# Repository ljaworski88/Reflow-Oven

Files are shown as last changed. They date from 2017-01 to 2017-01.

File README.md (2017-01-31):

# Reflow-Oven
My take on the diy relfow oven, inspired by the design by Karl Pitrich (karl@pitrich.com).

This reflow oven is still undergoing development, slowly, but works well enough to
bake some ICs. The reflowreader.py program is used to get a graphical output of the 
current temperature and setpoint (you will need to know which serial port the arduino
is connected to), it is written in python 2.7 and will need the correct interpreter.

The door does not open on its own yet and cannot autotune the PID but it can detect
the mains power frequency. The user will need to open the door manually for cooling.
Also fan control has not been implemented as my oven did not have any of that fanciness.

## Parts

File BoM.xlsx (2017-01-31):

Mfcr Part # | Description | cost | link
MAX31855 | Thermocouple IC | $4.50 | http://www.digikey.com/product-detail/en/MAX31855KASA%2B/MAX31855KASA%2B-ND/2591564
WB26K5069 | Convection Fan | $31.00 | http://www.ebay.com/itm/WB26K5069-GE-RANGE-OVEN-CONVECTION-MOTOR-FAN-/131715413430

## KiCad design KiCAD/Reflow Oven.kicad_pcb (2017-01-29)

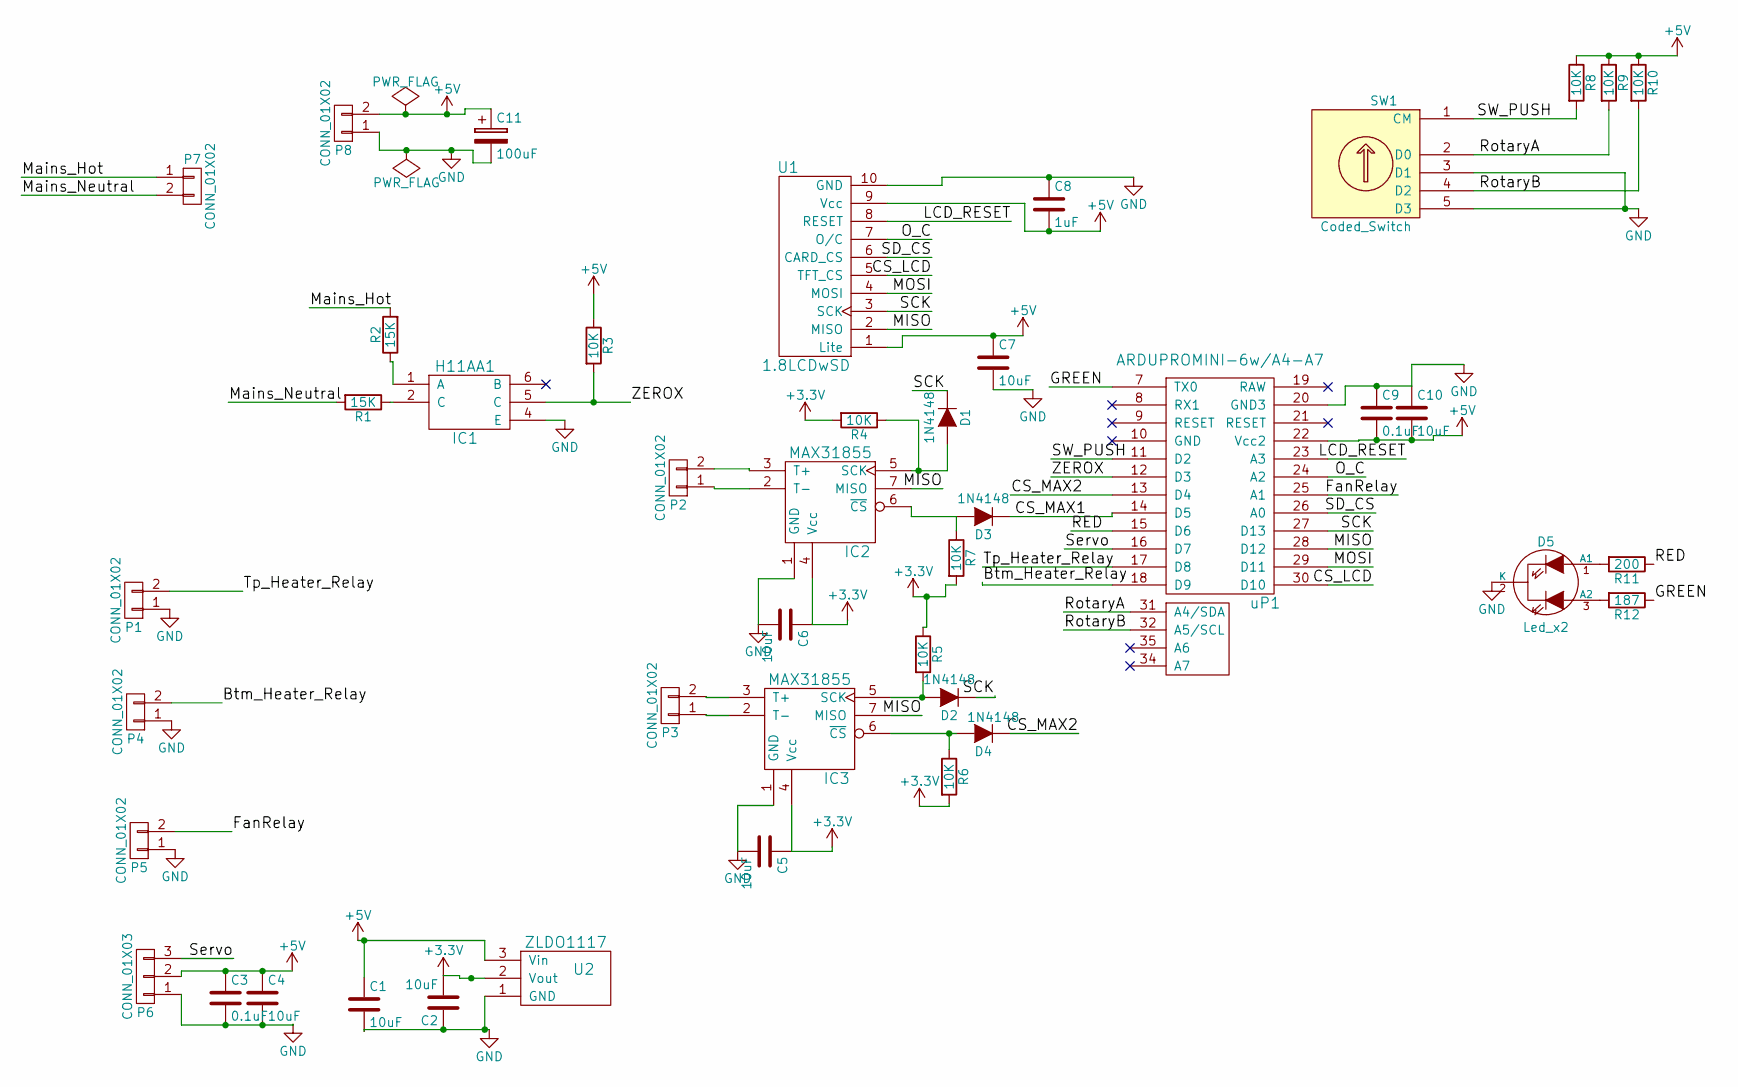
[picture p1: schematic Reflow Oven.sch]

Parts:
C1, C2, C4, C5, C6, C7, C10: 10uF; C_0402
C3, C9: 0.1uF; C_0402
C8: 1uF; C_0402
C11: 100uF; 10mm-THRU-ALUMINUM-CAP
D1, D2, D3, D4: 1N4148; SOD-123
D5: Led_x2; LED-5MM-3
IC1: H11AA1; SOIC-6
IC2, IC3: MAX31855; SOIC8
P1, P2, P3, P4, P5, P8: CONN_01X02; TerminalBlock_Pheonix_MPT-2.54mm_2pol
P6: CONN_01X03; SIP3
P7: CONN_01X02; TerminalBlock_Pheonix_PT-3.5mm_2pol
R1, R2: 15K; 1206
R3, R4, R5, R6, R7, R8, R9, R10: 10K; 0402
R11: 200; 0402
R12: 187; 0402
SW1: Coded_Switch; SF-ROTARY-ENCODER
U1: 1.8LCDwSD; 1X10
U2: ZLDO1117; DPAK
uP1: ARDUPROMINI-6w/A4-A7; ArduProMini-6

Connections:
+3V3: C2.2, C5.1, C6.1, IC2.4 (Vcc), IC3.4 (Vcc), R4.2, R5.1, R6.2, R7.2, U2.2 (Vout)
+5V: C1.1, C3.1, C4.1, C7.1, C8.2, C9.2, C10.2, C11.1, P6.2, P8.2, R3.1, R8.1, R9.1, R10.1, U1.1 (Lite), U1.9 (Vcc), U2.3 (Vin), uP1.22 (Vcc2)
/Btm_Heater_Relay: P4.2, uP1.18 (D9)
/CS_LCD: U1.5 (TFT_CS), uP1.30 (D10)
/CS_MAX1: D3.1 (K), uP1.14 (D5)
/CS_MAX2: D4.1 (K), uP1.13 (D4)
/FanRelay: P5.2, uP1.25 (A1)
/GREEN: R12.1, uP1.7 (TX0)
/LCD_RESET: U1.8 (RESET), uP1.23 (A3)
/MISO: IC2.7 (MISO), IC3.7 (MISO), U1.2 (MISO), uP1.28 (D12)
/MOSI: U1.4 (MOSI), uP1.29 (D11)
/Mains_Hot: P7.1, R2.2
/Mains_Neutral: P7.2, R1.2
/O_C: U1.7 (O/C), uP1.24 (A2)
/RED: R11.1, uP1.15 (D6)
/RotaryA: R9.2, SW1.2 (D0), uP1.31 (A4/SDA)
/RotaryB: R10.2, SW1.4 (D2), uP1.32 (A5/SCL)
/SCK: D1.1 (K), D2.1 (K), U1.3 (SCK), uP1.27 (D13)
/SD_CS: U1.6 (CARD_CS), uP1.26 (A0)
/SW_PUSH: R8.2, SW1.1 (CM), uP1.11 (D2)
/Servo: P6.3, uP1.16 (D7)
/Tp_Heater_Relay: P1.2, uP1.17 (D8)
/ZEROX: IC1.5 (C), R3.2, uP1.12 (D3)
GND: C1.2, C2.1, C3.2, C4.2, C5.2, C6.2, C7.2, C8.1, C9.1, C10.1, C11.2, D5.2 (K), IC1.4 (E), IC2.1 (GND), IC3.1 (GND), P1.1, P4.1, P5.1, P6.1, P8.1, SW1.3 (D1), SW1.5 (D3), U1.10 (GND), U2.1 (GND), uP1.20 (GND3)
unnamed: D1.2 (A), IC2.5 (SCK), R4.1
unnamed: D2.2 (A), IC3.5 (SCK), R5.2
unnamed: D3.2 (A), IC2.6 (~CS), R7.1
unnamed: D4.2 (A), IC3.6 (~CS), R6.1
unnamed: D5.1 (A1), R11.2
unnamed: D5.3 (A2), R12.2
unnamed: IC1.1 (A), R2.1
unnamed: IC1.2 (C), R1.1
unnamed: IC2.2 (T-), P2.1
unnamed: IC2.3 (T+), P2.2
unnamed: IC3.2 (T-), P3.1
unnamed: IC3.3 (T+), P3.2

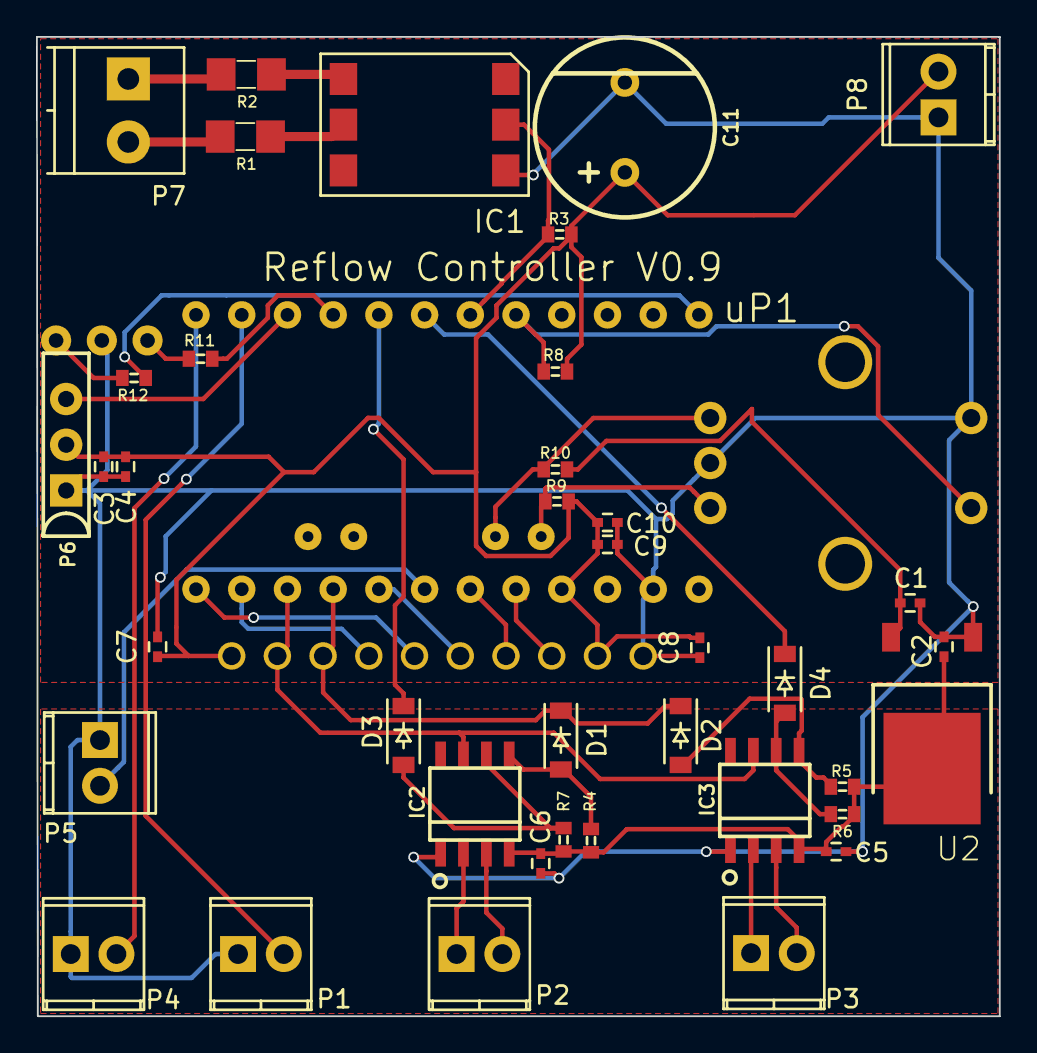
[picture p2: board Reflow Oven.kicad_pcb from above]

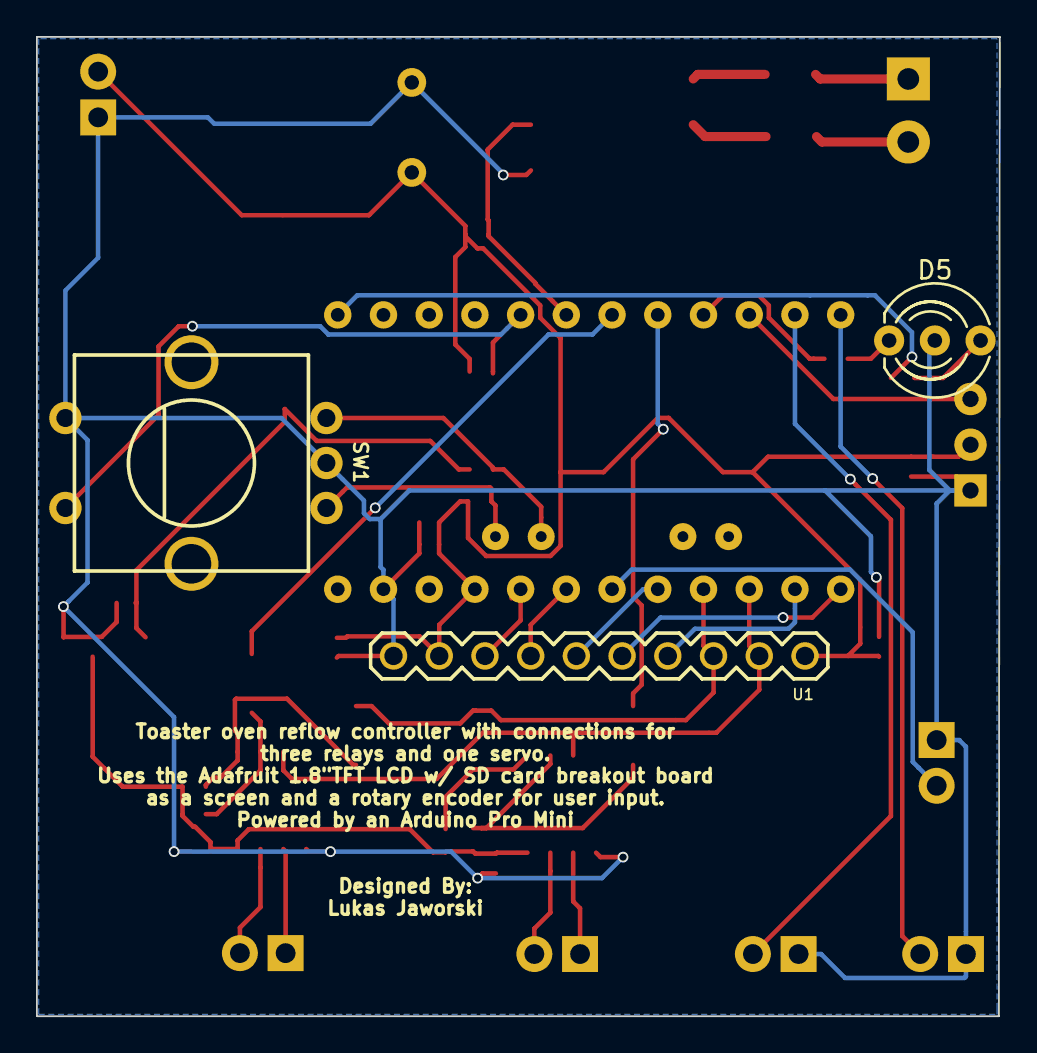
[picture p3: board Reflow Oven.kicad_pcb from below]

Board: 2 copper layers, 53.5 x 54.4 mm, 43 parts (3 on the bottom side), 36 nets.

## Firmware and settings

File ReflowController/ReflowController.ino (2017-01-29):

/* Reflow Oven Controller
 2016 Lukas Jaworski
 based on the Reflow Controller by Karl Pitrich
  v 0.7.2
*/ 

//-----------------------------------------------------------------------------
//Optional Defines
//-----------------------------------------------------------------------------

// #define AUTOPID true // autotune PID parameters
#define ZERO_X_CALIBRATION True

#ifdef ZERO_X_CALIBRATION
	#define CALIBRATION_CYCLES 12 //set how many calibration cyles are desired, the first two and last readings are thrown out due to inconsistant readings because of intialization and shutdown
#endif

//-----------------------------------------------------------------------------
//File Depencencies
//-----------------------------------------------------------------------------

#include <avr/io.h>
#include <PID_v1.h>
#include <Adafruit_GFX.h>
#include <Adafruit_ST7735.h>
#include <SPI.h>
#include <TimerOne.h>
#include <Servo.h>
#ifdef AUTOPID
	#include <PID_AutoTune_v0.h>
#endif

// ----------------------------------------------------------------------------
// Hardware Configuration
// ----------------------------------------------------------------------------

// 1.8" TFT via SPI

#define LCD_CS	10
#define LCD_OC	A2
#define LCD_RST	A3
#define SD_CS	A0


// Thermocouples

// Thermocouple via SPI-MAX31855
#define THERMOCOUPLE1_CS	5
#define THERMOCOUPLE2_CS	4//include later

//  Heater Solid State Relays

#define PIN_HEATER_TOP		9// SSR for the top heating elements- separate later
#define PIN_HEATER_BOTTOM	8// SSR for the bottom heating elements

//fan relay &| servo 

#define PIN_FAN		A1// SSR for the fan- This reflow oven has no fan
#define PIN_SERVO	7// servo control signal

// Rotary Encoder

#define ROTARY_A 	A4
#define ROTARY_B	A5
#define SW_PUSH		2

// Zero Crossing Detector

#define PIN_ZX		3 // pin for zero crossing detector
#define INT_ZX		digitalPinToInterrupt(PIN_ZX) // interrupt for zero crossing detector

// Indicator Light

#define RED		6
#define GREEN	0

//-----------------------------------------------------------------------------
// Profiles
//-----------------------------------------------------------------------------
typedef struct reflowProfile { //a complete reflow profile in terms temperaturs and temperature rates
	double	rampSoakRate;	//ramp to soak in degC/s
	double	soakLowTemp;	//temp in degC to start soak
	double	soakRate;		//gentle ramp during soak in degC/s
	double	soakHighTemp;	//temp in degC to stop soak and ramp to peak
	double	rampPeakRate;	//ramp to peak in degC/s
	double	peakTemp;		//peak temp in degC
	double	coolDownRate;	//cooling rate in degC/s
	double	safeTemp;		//temp in degC where oven is cool enough to work with
} reflowProfile;

typedef struct PID_constants { //a collection of PID constants
	double	Kp;
	double	Ki;
	double	Kd;
} PID_constants;

typedef struct PIDprofile { //a profile to adjust PID constants during reflow
	PID_constants	rampSoak;
	PID_constants	soak;
	PID_constants	rampPeak;
	PID_constants	coolDown;
} PIDprofile;

typedef struct currentParameters { //PID Input, Setpoint, and Output respectively
	double	avgTemp;
	double	setpoint;
	double	PID_output;
} currentParameters;

//-----------------------------------------------------------------------------
//TYPEDEFS
//-----------------------------------------------------------------------------

typedef enum reflowState { //state machine
	None     = 0,
	Idle     = 1,
	
	RampToSoak = 10,
	Soak,
	RampUp,
	RampDown,
	CoolDown,
	
	Complete = 20,
	
	Tune = 30
} reflowState;

typedef enum errorCode { //handle all currently known error states of the reflow oven
	NoError = 0,
	UnderTemp,
	OverTemp,
	BadReadings,
	NoMAX,
	VccShort,
	GndShort,
	OpenCircuit
} errorCode;


typedef union MAX31855_t { // thermocouple temp & status data, directly from the MAX31855
	uint32_t	value;
	uint8_t		bytes[4];

/*bits 31-18 hold the thermocouple data, 
bit 16 holds the fault bit (0 if no fault and 1 if there is one), this is not used at all in the code,
bits 15-4 hold the cold junction temperature, 
bits 2-0 explain the fault
*/   
} MAX31855_t;
 

typedef struct Thermocouple { // processed thermocouple data, status, and CS pin of the MAX31855
	double	temperature;
	uint8_t	stat;
	uint8_t	chipSelect;
} Thermocouple;

typedef struct rollingAvg { //holds the last ten actual temperature readings used in claclulating the rolling average, and keeps track of which position in the array needs to be updated next
	double	temps[10];
	uint8_t	position = 0;
} rollingAvg;

typedef struct cycleCount {//the "cycle counter" is how the PID output is translated into heater on/off times
	uint8_t	tensPlace;
	uint8_t	thirds;
	uint8_t	positionThirds;
	uint8_t	positionTens;
} cycleCount;

//-------------------------------------------------------------------------------
//Global Variables
//-------------------------------------------------------------------------------

const uint8_t		uSecPerTick = 100; //sets the timer tick rate that is used throughout the program, if you want to change this go over the code very carefully, especially the ISRs
const double		uSecPerSec = 0.0001;//conversion factor for the timer 0.0001sec = 100 usec
const uint32_t		updateTime = 10000; //update the setpoints every 1s - the updateTime variable is tied to the 100usec counter

volatile bool       cycleFinished = true; //indicates if the current "PWM" cycle is finished
volatile bool		offCounter = false; //the state of the countdown timer to turn off the SSR.
volatile uint8_t	offTimerTicks = 0;
volatile uint32_t	timerTicks = 0; //100usec timer keeper (no overflow detection)
// volatile uint32_t	zeroXticks = 0; //counts the zero crossing events, used in PID control
uint32_t			lastTimerTicks = 0;
uint32_t			lastPIDticks = 0;//used to ensure that the PID computes every time a heating "cycle" is finnished
uint8_t				usecPerZX = 83;//8.3ms (or 83 ticks @ 100us/tick) between ZeroX for 60Hz mains, 
									//sub in 10 for 50Hz. 
									//This value will be updated if a calibration is performed.
Thermocouple		thermoInput1; //intialize thermocouple 1
// Thermocouple		thermoInput2; //intialize thermocouple 2
uint8_t				servoPos = 0;
Servo				doorServo;
const uint32_t 		thermoUpdateTime = 250;//checks the temperature every 25ms so that it doesn't over tax the thermocouple IC
uint32_t			lastThermoUpdate;
reflowProfile		curProfile = {1.1, 135.0, 0.6, 165.0, 1.3, 225.0, 2.0, 50.0}; //the current reflow profile (also the only)
PIDprofile			curPIDprofile = {{1.1, 0.5, 30},{1.0, 0.1, 35.0},{3.0, 0.5, 5.0},{7.0, 0.01, 2.0}}; /*{{1.1, 0.101, 17.0},{1.0, 0.1, 18.0},{1.1, 0.1, 17.0},{7.0, 0.01, 2.0}}; //Profile of PID constants */
currentParameters	curParameters; //the current temp, setpoint, and pid output
reflowState			curOvenState = None; //current phase of the reflow cycle
rollingAvg			curRollingAvg; //a collection of past temp readings used in the rolling average
volatile cycleCount	cycleCounter = {0, 0, 0, 0}; //used to control heater on/off timings
volatile errorCode	curError = NoError;//Error code variable that handles all errors in the machine

PID					tempPID(&(curParameters.avgTemp),&(curParameters.PID_output),&(curParameters.setpoint),curPIDprofile.rampSoak.Kp,curPIDprofile.rampSoak.Kp,curPIDprofile.rampSoak.Kp,DIRECT);

#ifdef ZERO_X_CALIBRATION //These additional variables will be needed only if a ZeroX calibration is performed.
	volatile uint16_t	calibrationCycle = 0;
	volatile uint32_t	lastCalibrationTicks = 0;
	bool				calibrationFinished = false;
	uint16_t			calibrationArray[CALIBRATION_CYCLES];
	double				calibrationAvg = 0.0;
#endif

//-----------------------------------------------------------------------------
//FUNCTIONS
//-----------------------------------------------------------------------------

void readThermocouple(Thermocouple* input, volatile errorCode& ErrorCode) { //function to read the data from the MAX31855 and handle any errors that may arrise
	MAX31855_t readSensor;

	// uint8_t lcdState = digitalRead(LCD_CS);
	// digitalWrite(LCD_CS, HIGH);
	SPI.beginTransaction(SPISettings(4000000,MSBFIRST,SPI_MODE0));
	digitalWrite(input->chipSelect, LOW);
	for (int8_t i = 3; i >= 0; i--){
		readSensor.bytes[i] = SPI.transfer(0);
	}
	digitalWrite(input->chipSelect, HIGH);
	SPI.endTransaction();
	if (readSensor.value == 0){ //if nothing but zeroes is read then the MAX31855 is not connected or there is something seriously wrong, error is thrown
		ErrorCode = NoMAX;
	return;
	}
	input->stat = readSensor.bytes[0] & 0b111;
	if (input->stat){//this is the error handling portion which reads the MAX31855 error codes and passes them along to the main program
		switch (input->stat) {
			case 0b001:
				ErrorCode = OpenCircuit;
				return;
			case 0b010:
				ErrorCode = GndShort;
				return;
			case 0b100:
				ErrorCode = VccShort;
				return;
		}
	}
	uint16_t value = (readSensor.value >> 18) & 0x3FFF; //shift to the correct alignment for the temp data  
	input->temperature = (double) value * 0.25;
	// digitalWrite(LCD_CS, lcdState);
}

void openDoor(void){ 
	//use servo to open door as much as the servo will allow, also turns on a red indicator led
	digitalWrite(RED, HIGH);
	for (servoPos; servoPos<180; servoPos++){
		doorServo.write(servoPos);
		delay(100);
	}
}

void closeDoor(void){
	//use servo to fully close door
	for (servoPos; servoPos>0; servoPos--){
		doorServo.write(servoPos);
		delay(100);
	}
	
}

void indicateDone(bool errorFlag = false){//currently a dummy function
	//indicate that the reflow is complete (Use LED AND buzzer to indicate that reflow is complete)
	
}

void updateSetpoints(reflowState& ovenState, reflowProfile Profile, currentParameters& Params, PID& PID, PIDprofile PIDprofile){ //This function updates the setpoints of the reflow profile at the specified updateTime (which is counted in 100usec ticks)
	uint32_t timeSinceUpdate = timerTicks-lastTimerTicks;
	if (timeSinceUpdate>updateTime){//checks to see if there has been enough time since the last update to once again update the setpoints.
		if (ovenState>Idle && ovenState<RampDown){//Checks the reflow to see if it is in the heat up phase and adjusts the setpoints according to the programed profile.
			switch(ovenState) {
				case RampToSoak:
					Params.setpoint += Profile.rampSoakRate*double(timeSinceUpdate)*(uSecPerSec);
					if (Params.setpoint > Profile.soakLowTemp){
						ovenState = Soak;
						PID.SetTunings(curPIDprofile.soak.Kp,curPIDprofile.soak.Kp,curPIDprofile.soak.Kp);
					}
				break;
				
				case Soak:
					Params.setpoint += Profile.soakRate*double(timeSinceUpdate)*(uSecPerSec);
					if (Params.setpoint > Profile.soakHighTemp){
						ovenState = RampUp;
						PID.SetTunings(curPIDprofile.rampPeak.Kp,curPIDprofile.rampPeak.Kp,curPIDprofile.rampPeak.Kp);
					}
				break;
				
				case RampUp:
					Params.setpoint += Profile.rampPeakRate * double(timeSinceUpdate)*(uSecPerSec);
					if (Params.setpoint > (Profile.peakTemp - 5.0)){
						PID.SetMode(MANUAL);
						Params.PID_output = 0;
					}
					if (Params.setpoint > Profile.peakTemp){
						openDoor();
						ovenState = RampDown;
						PID.SetTunings(curPIDprofile.coolDown.Kp,curPIDprofile.coolDown.Kp,curPIDprofile.coolDown.Kp);
					}
				break;
			}
		}
		else if (ovenState>=RampDown && ovenState<Complete){// This section of the code deal with the cooling portion of the reflow process
			switch(ovenState) {
				case RampDown:
					Params.setpoint -= Profile.coolDownRate*double(timeSinceUpdate)*(uSecPerSec);
					if (Params.setpoint < Profile.safeTemp){
						ovenState = CoolDown;
						PID.SetMode(MANUAL);
						Params.PID_output = 0;
					}
				break;
				
				case CoolDown:
					Params.setpoint = 0.0;
					ovenState = Complete;
				break;
			}
		}
		else {
			if(ovenState == Complete){
				//indicateDone();
				ovenState = Idle;
			}
		}
		
		lastTimerTicks = timerTicks;	
	}

}

void rollAverage(rollingAvg& rollAvg, currentParameters& Params, volatile errorCode& ErrorCode){//takes a new temperature reading and averages it with the previous 9 readings
	uint32_t timeSinceUpdate = timerTicks-lastThermoUpdate;//The main loop is faster than the update time of the MAX31855 IC so a delay had to be added
	static uint8_t errorTempCount = 0;
	double curReading;
	if (timeSinceUpdate>thermoUpdateTime){
		readThermocouple(&thermoInput1, ErrorCode);
		curReading = thermoInput1.temperature;
		if ((curReading - Params.avgTemp) > 10 || (curReading - Params.avgTemp) < -10){//this checks if an individual reading is more than 10C different than the average, indicating a bad reading (should be impossible to move that much in a couple ms)
			errorTempCount += 3;
			if (errorTempCount >= 15){//only throw an error if the bad readings get excessive
				ErrorCode = BadReadings;
				return;
			}
		}
		else if (errorTempCount > 0){
			errorTempCount --;
		}
		
		//the next few lines handle the averaging of the temperature *note that only one value is removed and added at a time to save caluclation cycles
		
		Params.avgTemp -= rollAvg.temps[rollAvg.position]/10.0; //removes the reading that was at this postion previously (the average adjusted amount)
		rollAvg.temps[rollAvg.position] = curReading;
		Params.avgTemp += curReading/10.0; //adds in the current reading into the average
		rollAvg.position ++;
		if (rollAvg.position > 9){
			rollAvg.position = 0;
		}
		curReading = Params.avgTemp - Params.setpoint;//repurpose the curReading variable to see if the current average is too far from the setpoint, it is being repurposed because I am getting close to the heap limit
		if (curReading>50.0 || curReading<-50.0){
			if (curReading>10){
				ErrorCode = OverTemp;
				if (curOvenState>=RampDown && curOvenState<=Complete){
					ErrorCode = NoError;
				}
			}
			else{
				ErrorCode = UnderTemp;
			}
		}
		lastThermoUpdate = timerTicks;
	}
	
}

void pinSetup(){//Self explanitory, sets up the pin configuration for proper communication and control
	pinMode(THERMOCOUPLE1_CS, OUTPUT);
	digitalWrite(THERMOCOUPLE1_CS, HIGH);
	pinMode(THERMOCOUPLE2_CS, OUTPUT);
	digitalWrite(THERMOCOUPLE2_CS, HIGH);
	pinMode(PIN_HEATER_BOTTOM, OUTPUT);
	digitalWrite(PIN_HEATER_BOTTOM, LOW);
	pinMode(PIN_HEATER_TOP, OUTPUT);
	digitalWrite(PIN_HEATER_TOP, LOW);
	pinMode(PIN_FAN, OUTPUT);
	digitalWrite(PIN_FAN, LOW);
	pinMode(RED, OUTPUT);
	digitalWrite(RED, LOW);
	// pinMode(GREEN, OUTPUT); //The green LED is hooked up to the TX of the Arduino's serial (They share the same pin) so if a serial output is desired the serial communications must be turned off to function correctly
	// digitalWrite(GREEN, LOW);
	pinMode(LCD_CS, OUTPUT);
	digitalWrite(LCD_CS, HIGH);
	pinMode(SD_CS, OUTPUT);
	digitalWrite(SD_CS, HIGH);
	pinMode(LCD_OC, OUTPUT);
	digitalWrite(LCD_OC, LOW);
	pinMode(LCD_RST, OUTPUT);
	digitalWrite(LCD_RST, LOW);
	pinMode(ROTARY_A, INPUT);
	pinMode(ROTARY_B, INPUT);
	pinMode(SW_PUSH, INPUT);
	doorServo.attach(PIN_SERVO);
}

double initalTemp(rollingAvg& rollAvg, volatile errorCode ErrorCode){//Gets an intial value for the oven temperature
	double averageTemp = 0;
	for (uint8_t i = 0; i <10; i++){//the full array is loaded on initalization to ensure a decent average
		readThermocouple(&thermoInput1, ErrorCode);
		rollAvg.temps[i] = thermoInput1.temperature;
		averageTemp += thermoInput1.temperature/10.0;
		delay(25);
	}
	lastThermoUpdate = timerTicks;
	return averageTemp;
}

void updatePID(PID& PID, currentParameters Params, volatile cycleCount& cycleSet, volatile bool& update){//updates the PID output and set up the next 1/2sec of heater function (which runns on a % of the 30 AC cycles that should happen in that time)
	//this code only responds to changes in 3% on time segments, so a change of at least 3% is needed to see an effect (i.e. 90%=91%=92%<93%)
	uint8_t intOutput;
	uint32_t now = millis();
	cli(); //interrupts are disabled here because they were interferring with the serial print function
	if(update){
		// PID.SetSampleTime(now-lastPIDticks);
		PID.Compute(); //the output is set from 0-33, so that each whole number change of the PID actually has an effect on heater on time
		intOutput = int(Params.PID_output)*3; //this makes it so the next part sees a number from 0-99%
		// Serial.println("Params.PID_output");
		// Serial.println(intOutput);
		// Serial.println("Params.setpoint");
		// Serial.println(Params.setpoint);
		// Serial.println("Params.avgTemp:");
		// Serial.println(Params.avgTemp);
		Serial.print(intOutput);//This serial data is feed into a python program to graph the datapoints
		Serial.print(",");
		Serial.print(Params.setpoint);
		Serial.print(",");
		Serial.println(Params.avgTemp);
		cycleSet.tensPlace = intOutput / 10; //the 30 cycles are divided into 3 10 subcycle segments, with the tens place indicating how many of each of the 3 subcycles will be on for (0%-9% = 0; 10%-19% = 1 ... 90%-99% = 9; and 100% does not exist technically but is functionally the same as a 99%)
		cycleSet.thirds = (intOutput % 10) / 3; //will turn on an extra cycle based on the ones place of the PID output. (0%-2% = 0 extra cycles; 3%-5% = 1 extra cycles ... 7%-9% = 3 extra cycles: this ends up meaning that 9% and 10%; 19% and 20%; etc. are equivilent in terms of heater on time)
		cycleSet.positionThirds = 0;
		cycleSet.positionTens = 0;
		update = false;
		lastPIDticks = millis();        
    }
	sei();
}

void checkErrors(volatile errorCode ErrorCode){//This function checks for any reflow ending errors, shuts off the oven, and spits out an error code
    if (curOvenState != Idle || curOvenState != Complete){
		if (ErrorCode){
			cli();//interrupts are no longer need at this point so they are disabled
			digitalWrite(PIN_HEATER_BOTTOM, LOW); //Turns off the heating elements
			switch(ErrorCode){
				case UnderTemp:
					while(1){
						Serial.println("UT"); //Undertemp
						delay(1000);
					}
					break;
				case OverTemp:
					while(1){
						Serial.println("OT"); //Overtemp
						delay(1000);
					}
					break;
				case BadReadings:
					while(1){
						Serial.println("BR"); //Too many bad readings from the MAX31855
						delay(1000);
					}
					break;
				case NoMAX:
					while(1){
						Serial.println("NM"); //no MAX31855 detected
						delay(1000);
					}
					break;
				case VccShort:
					while(1){
						Serial.println("VS"); //MAX31855 Vcc short error
						delay(1000);
					}
					break;
				case GndShort:
					while(1){
						Serial.println("GS");//MAX31855 Gnd short error
						delay(1000);
					}
					break;
				case OpenCircuit:
					while(1){
						Serial.println("OC");//MAX31855 Open Circuit error
						delay(1000);
					}
					break;
			}
		}

	}
}

//-------------------------------------------------------------------------------
//ISRs
//-------------------------------------------------------------------------------

void timerISR(void){//The timer is used for the ZeroX calibration and to turn off the relay slightly before the zeroX event to ensure the triac stays off when it is supposed to
#ifdef ZERO_X_CALIBRATION 
	if(!calibrationFinished){
		timerTicks++;
	}
	else {
#endif
		if(offCounter && (offTimerTicks > usecPerZX - 10 )){//turns the relay off about 1ms before the start of an off cycle to ensure the triac stays off
		//currently the code will go through the offTimer code EVERY time the next cycle is supposed to be off, this is inefficent but does not cause a problem in the 16MHz Arduinos tested, slower clocked chips may encounter problems (this is untested though)
			digitalWrite(PIN_HEATER_BOTTOM, LOW);
			offCounter = false; //the off timer is turned off once it has completed its function.
			offTimerTicks = 0;
		}
		else if(offCounter){
			offTimerTicks++;
		}
	timerTicks++;
#ifdef ZERO_X_CALIBRATION
	}
#endif
	
}

//note: the zeroXingISR needs an external interrupt to run. If you cannot hook up a ZeroX detector (I recommend the H11AA1 for this) then use a 555 timer and set
// it to run at approximately your desired frequency. Without a true ZeroX detector this code won't run as well but if you are unsure about working with mains
//power it will keep you safer (still be careful around the relay).
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
void loop(){
	// Serial.println(calibrationAvg);
	updateSetpoints(curOvenState, curProfile, curParameters, tempPID, curPIDprofile);
	rollAverage(curRollingAvg, curParameters, curError);
	checkErrors(curError);
	updatePID(tempPID, curParameters, cycleCounter, cycleFinished);
}

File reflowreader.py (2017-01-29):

import serial
import numpy
import matplotlib.pyplot as plt
from drawnow import *

setpoints = []
avgTemp = []
PIDoutput = []
tempData = serial.Serial('COM3', 115200)
plt.ion()
tempBuffer = 0

def makeFig():
    plt.ylim(20, 250)
    plt.xlim(0, 360)
    plt.title('Reflow Controller Temp and Setpoint Data')
    plt.grid(True)
    plt.ylabel('Temp C')
    plt.plot(setpoints, 'ro-', label='Setpoints')
    plt.plot(avgTemp, 'b^-', label='Temperature')
    plt.legend(loc='upper left')
    plt2 = plt.twinx()
    plt.ylim(0,100)
    plt2.plot(PIDoutput, 'go-', label = 'PID Output')
    plt2.set_ylabel('PID')
    plt2.ticklabel_format(useOffset = False)
	
    

while True:
    while (tempData.inWaiting()==0):
        pass
    dataString = tempData.readline()
    dataArray = dataString.split(',')
    tempPID = float(dataArray[0])
    tempSetpoint = float(dataArray[1])
    tempTemp = float(dataArray[2])
    PIDoutput.append(tempPID)
    setpoints.append(tempSetpoint)
    avgTemp.append(tempTemp)
    drawnow(makeFig)
    plt.pause(0.000001)
    tempBuffer += 1
    if(tempBuffer > 360):
         PIDoutput.pop(0)
         setpoints.pop(0)
         avgTemp.pop(0)
	
